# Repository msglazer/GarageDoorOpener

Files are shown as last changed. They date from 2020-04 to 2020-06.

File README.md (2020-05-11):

# GarageDoorOpener
Garage door opener keyfob replacement that can detect door position and allows for OK google commands. As well as a distance sensor and LEDs to show distance from garage wall.

## Hardware:
### Power Board

Features:
* 120V AC/DC converter to 24V, 20W output
* Two reed switch connectors 
* One relay control connector
* RJ45 connector for cable to control board

### Control Board

Features:
* Particle Boron Microcontroller with cellular connectivity
* 24V to 5W switching regulator
* ToF sensor for range finding
* LED header for visualizing distance
* RJ45 connector for power/control

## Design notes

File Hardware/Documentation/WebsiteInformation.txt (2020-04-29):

https://www.smps.us/pcbtracespacing.html - AC Creepage/Spacing Information
https://www.amazon.com/Aleph-DC-1561-Surface-Magnetic-Contact/dp/B00LYCUSBY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 - Reed switch, magnet combo

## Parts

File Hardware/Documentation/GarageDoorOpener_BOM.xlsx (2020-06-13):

Board | Need | Number | Unit Qty | RefDes | Value | Manufacturer | Dist. Part # | Mfg Part # | Price Each | Total Price | Description | Package | Type | Datasheet
Control | Have | 1 | 1 | U1 | 4G MCU | Particle | 1878-1023-ND | BRN402 | 49.28 | 49.28 | BORON LTE Microcontroller | Feather | Thru-hole | https://media.digikey.com/pdf/Data%20Sheets/Particle%20PDFs/Boron_LTE_Web.pdf
Control | Need | 2 | 1 | U2 | Switching Regulator | Texas Instruments | 296-TPS56637RPARCT-ND | TPS56637RPAR | 3.50 | 3.50 | Buck Switching Regulator IC Positive Adjustable 0.6V 1 Output 6A 10-PowerVFQFN | 10-PowerVFQFN | SMD | http://www.ti.com/general/docs/suppproductinfo.tsp?distId=10
Control | Need | 3 | 1 | U3 | Solid State Relay | IXYS Integrated Circuits Division | CLA221-ND | CPC1002N | 1.08 | 1.08 | Solid State SPST-NO (1 Form A) 4-SOP (0.150", 3.81mm) | 4-SOP (0.150", 3.81mm) | SMD | http://www.ixysic.com/home/pdfs.nsf/www/CPC1002N.pdf/$file/CPC1002N.pdf
Control | Need | 4 | 1 | U4 | ToF Sensor | STMicroelectronics | 497-17764-1-ND | VL53L1CXV0FY/1 | 6.43 | 6.43 | Optical Sensor 157.480" (4m) I²C Output | LGA-12 | SMD | https://www.mouser.com/datasheet/2/389/dm00452094-1799360.pdf
Control | Need | 5 | 1 | U5 | Level Shifter | Texas Instruments | 296-22862-6-ND | TXB0102DCUR | 0.71 | 0.71 | Voltage Level Translator Bidirectional 1 Circuit 2 Channel 100Mbps 8-VSSOP | 8-VSSOP | SMD | http://www.ti.com/general/docs/suppproductinfo.tsp?distId=10
Control | Need | 6 | 2 | Q1,Q2 | NMOS FET | Diodes Inc | DMG1012T-7DICT-ND | DMG1012T-7 | 0.29 | 0.58 | N-Channel 20V 630mA (Ta) 280mW (Ta) Surface Mount SOT-523 | SOT-523 | SMD | https://www.diodes.com/assets/Datasheets/ds31783.pdf
Control | Need | 7 | 1 | Q3 | PMOS FET | Nexperia USA Inc. | 1727-2310-1-ND | PMV65XPEAR | 0.36 | 0.36 | P-Channel 20V 2.8A (Ta) 480mW (Ta), 6.25W (Tc) Surface Mount TO-236AB | SOT-23-3 | SMD | https://assets.nexperia.com/documents/data-sheet/PMV65XPEA.pdf
Control | Need | 8 | 1 | L1 | Switching regulator inductor | Taiyo Yuden | 587-2892-1-ND | NRS4018T3R3MDGJ | 0.29 | 0.29 | 3.3µH Shielded Wirewound Inductor 2A 66mOhm Max Nonstandard | 4mm x 4mm | SMD | https://www.yuden.co.jp/productdata/catalog/wound04_e.pdf
Control | Have | 9 | 1 | D1 | Green LED | Würth Elektronik | 732-4986-1-ND | 150080VS75000 | 0.18 | 0.18 | Green 570nm LED Indication - Discrete 2V 0805 (2012 Metric) | 0805 | SMD | https://katalog.we-online.de/led/datasheet/150080VS75000.pdf
Control | Have | 10 | 1 | D2 | Red LED | Würth Elektronik | 732-4985-1-ND | 150080SS75000 | 0.18 | 0.18 | Red 630nm LED Indication - Discrete 1.9V 0805 (2012 Metric) | 0805 | SMD | https://katalog.we-online.de/led/datasheet/150080SS75000.pdf
Control | Need | 11 | 3 | D3,D4,D5 | TVS diode array (2 channel) | Toshiba Semiconductor and Storage | DF3A5.6LFULFCT-ND | DF3A5.6LFU,LF | 0.29 | 0.87 | 3V (Typ) Clamp 5A (8/20µs) Ipp Tvs Diode Surface Mount 7-XSON (1.1x2.1) | 7-XSON | SMD | https://assets.nexperia.com/documents/data-sheet/PUSB3FR6.pdf
Control | Have? | 12 | 3 | C1,C2,C3 | 4.7uF 50V | Murata Electronics | 490-10751-1-ND | GRM21BR61H475KE51L | 0.41 | 1.23 | 4.7µF ±10% 50V Ceramic Capacitor X5R 0805 (2012 Metric) | 0805 | SMD | https://search.murata.co.jp/Ceramy/image/img/A01X/G101/ENG/GRM21BR61H475KE51-01.pdf
Control | Have? | 13 | 1 | C4 | 0.1uF 50V | KEMET | 399-7845-1-ND | C0603C104M5RACTU | 0.10 | 0.10 | 0.1µF ±20% 50V Ceramic Capacitor X7R 0603 (1608 Metric) | 0603 | SMD | https://api.kemet.com/component-edge/download/datasheet/C0603C104M5RACTU.pdf
Control | Have | 14 | 4 | C5,C6,C16,C17 | 1uF 10V | Samsung Electro-Mechanics | 1276-1182-1-ND | CL10A105KP8NNNC | 0.10 | 0.40 | 1µF ±10% 10V Ceramic Capacitor X5R 0603 (1608 Metric) | 0603 | SMD | https://media.digikey.com/pdf/Data%20Sheets/Samsung%20PDFs/CL10A105KP8NNNC_Spec.pdf
Control | Have | 15 | 2 | C7,C12 | 0.1uF 16V | KEMET | 399-1099-1-ND | C0603C104M4RACTU | 0.10 | 0.20 | 0.1µF ±20% 16V Ceramic Capacitor X7R 0603 (1608 Metric) | 0603 | SMD | https://api.kemet.com/component-edge/download/datasheet/C0603C104M4RACTU.pdf
Control | Have? | 16 | 1 | C8 | 100pF 10V | Würth Elektronik | 732-7922-1-ND | 885012206003 | 0.10 | 0.10 | 100pF ±10% 10V Ceramic Capacitor X7R 0603 (1608 Metric) | 0603 | SMD | https://katalog.we-online.de/pbs/datasheet/885012206003.pdf
Control | Have | 17 | 2 | C9,C10 | 22uF 10V | Taiyo Yuden | 587-5464-1-ND | LMK212BBJ226MG-T | 0.30 | 0.60 | 22µF ±20% 10V Ceramic Capacitor X5R 0805 (2012 Metric) | 0805 | SMD | https://ds.yuden.co.jp/TYCOMPAS/ut/detail?pn=LMK212BBJ226MG-T%20&u=M
Control | Have? | 18 | 2 | C11,C13 | 4.7uF 10V | Taiyo Yuden | 587-1441-1-ND | LMK107BJ475KA-T | 0.19 | 0.38 | 4.7µF ±10% 10V Ceramic Capacitor X5R 0603 (1608 Metric) | 0603 | SMD | https://ds.yuden.co.jp/TYCOMPAS/ut/detail?pn=LMK107BJ475KA-T%20%20&u=M
Control | Have | 19 | 2 | C14,C15 | 2.2uF Cap
Control | Need | 20 | 3 | R1,R3,R4 | 649 ohm 1% | Stackpole Electronics | RMCF0603FT649RCT-ND | RMCF0603FT649R | 0.10 | 0.30 | 649 Ohms ±1% 0.1W, 1/10W Chip Resistor 0603 (1608 Metric) Automotive AEC-Q200 Thick Film | 0603 | SMD | https://www.seielect.com/catalog/sei-rmcf_rmcp.pdf
Control | Have | 21 | 11 | R2,R5,R6,R7,R9,R14,R15,R24,R26,R28 | 10K ohm 5% | Stackpole Electronics | RMCF0603JT10K0CT-ND | RMCF0603JT10K0 | 0.10 | 1.10 | 10 kOhms ±5% 0.1W, 1/10W Chip Resistor 0603 (1608 Metric) Automotive AEC-Q200 Thick Film | 0603 | SMD | https://www.seielect.com/catalog/sei-packaging.pdf
Control | Have | 22 | 1 | R11 | 10K ohm 1% | Yageo | 311-10.0KHRCT-ND | RC0603FR-0710KL | 0.10 | 0.10 | 10 kOhms ±1% 0.1W, 1/10W Chip Resistor 0603 (1608 Metric) Moisture Resistant Thick Film | 0603 | SMD | https://www.yageo.com/upload/media/product/productsearch/datasheet/rchip/PYu-RC_Group_51_RoHS_L_10.pdf
Control | Need | 23 | 1 | R8 | 20K ohm 1% | Yageo | 311-20.0KHRCT-ND | RC0603FR-0720KL | 1.00 | 1.00 | RES SMD 20K OHM 1% 1/10W 0603 | 0603 | SMD | https://www.yageo.com/upload/media/product/productsearch/datasheet/rchip/PYu-RC_Group_51_RoHS_L_10.pdf
Control | Need | 24 | 1 | R10 | 73.2K ohm 1% | KOA Speer Electronics, Inc. | 2019-RK73H1JTTD7322FCT-ND | RK73H1JTTD7322F | 0.10 | 0.10 | 73.2 kOhms ±1% 0.1W, 1/10W Chip Resistor 0603 (1608 Metric) Automotive AEC-Q200, Moisture Resistant Thick Film | 0603 | SMD | http://www.koaspeer.com/pdfs/RK73H.pdf
Control | Have | 25 | 2 | R12,R13 | 4.7K ohm 5% | Yageo | 311-4.7KGRCT-ND | RC0603JR-074K7L | 0.10 | 0.20 | 4.7 kOhms ±5% 0.1W, 1/10W Chip Resistor 0603 (1608 Metric) Moisture Resistant Thick Film | 0603 | SMD | https://www.yageo.com/upload/media/product/productsearch/datasheet/rchip/PYu-RC_Group_51_RoHS_L_10.pdf
Control | Have | 26 | 6 | R16,R17,R18,R19,R20,R21 | 0 ohm | Yageo | 311-0.0GRCT-ND | RC0603JR-070RL | 0.10 | 0.60 | 0 Ohms Jumper 0.1W, 1/10W Chip Resistor 0603 (1608 Metric) Moisture Resistant Thick Film | 0603 | SMD | https://www.yageo.com/upload/media/product/productsearch/datasheet/rchip/PYu-RC_Group_51_RoHS_L_10.pdf
Control | Have | 27 | 3 | R22.R23,R25 | 226 ohm
Control |  | 28 | 1 | J1 |  | LED header |  |  |  | 0.00
Control | Need | 29 | 1 | J2 | RJ45 Connector | Amphenol ICC (FCI) | 609-1046-ND | 54602-908LF | 0.62 | 0.62 | Jack Modular Connector 8p8c (RJ45, Ethernet) 90° Angle (Right) Unshielded Cat3 | RJ45 | Thru-hole | https://cdn.amphenol-icc.com/media/wysiwyg/files/documentation/datasheet/inputoutput/io_modularjack.pdf
Control | Need | 30 | 1 | PWR_IN1 | power inlet | Qualtek | Q840-ND | 770W-X2/13 | 0.77 | 0.77 | Power Entry Connector Receptacle, Male Pins IEC 320-C8 Panel Mount, Snap-In | 24.5x12.5 | Panel Mount | http://www.qualtekusa.com/images/AC_Receptacles/pdfs/770wx213.pdf
Control | Need | 31 | 1 | CABLE1 | 120V cord | Qualtek | Q536-ND | 223082-01 | 3.95 | 3.95 | 6.00' (1.83m) Power Cord Black NEMA 1-15P, Polarized To IEC 320-C7, Polarized SPT-2 | Cable | Thru-hole | http://www.qualtekusa.com/images/Power%20Cords/PDF%20Files/22308201.pdf
Control | Have | 32 | 1 | ANT1 | 4G antenna | Taoglas Limited | 931-1329-ND | FXUB63.07.0150C | 9.82 | 9.82 | 850MHz, 1.575GHz, 1.8GHz, 2.1GHz, 2.4GHz, 2.6GHz GPS, LTE, Wi-Fi Flat Patch RF Antenna 698MHz | flex PCB | UFL | https://cdn.taoglas.com/datasheets/FXUB63.07.0150C.pdf
Control | Have | 33 | 1 | PCB1 |  | OshPark |  |  | 11.25 | 11.25 |  | Rigid PCB
Control | Need | 34 | 1 | LEDSTRIP1 |  | SparkFun | COM-14015 |  | 8.03 | 8.03 | LED RGB Strip - Addressable, 1m (APA102)
Power | Need | 1 | 1 | PS1 |  | Mean Well USA | 1866-3040-ND | IRM-20-24 | 11.50 | 11.50 | Enclosed AC DC Converters 1 Uitgang 24V 900mA 85 ~ 264 VAC, 120 ~ 370 VDC Input | 4-DIP Module, 4 Leads | Thru-hole | https://www.meanwell.com/Upload/PDF/IRM-20/IRM-20-SPEC.PDF
Power | Need | 2 | 1 | J1 | 2pin AC Input | Phoenix Contact | 277-1721-ND | 1984617 | 0.48 | 0.48 | 2 Position Wire to Board Terminal Block Horizontal with Board 0.138" (3.50mm) Through Hole | 3.5mm pitch | Thru-hole | https://media.digikey.com/pdf/Data%20Sheets/Phoenix%20Contact%20PDFs/Combicon%20Compact%20Series.pdf
Power | Have? | 3 | 3 | J2,J3,J4 | 2pin JST | JST Sales America Inc | 455-1719-ND | S2B-PH-K-S(LF)(SN) | 0.17 | 0.51 | Connector Header Through Hole, Right Angle 2 position 0.079" (2.00mm) | 2pin | Thru-hole | http://www.jst-mfg.com/product/pdf/eng/ePH.pdf
Power | Need | 4 | 1 | J3 | RJ45 Connector | Amphenol ICC (FCI) | 609-1046-ND | 54602-908LF | 0.62 | 0.62 | Jack Modular Connector 8p8c (RJ45, Ethernet) 90° Angle (Right) Unshielded Cat3 | RJ45 | Thru-hole | https://cdn.amphenol-icc.com/media/wysiwyg/files/documentation/datasheet/inputoutput/io_modularjack.pdf
Power | Need | 5 | 4 | C1,C2,C3,C4 | 22uF 35V | TDK Corporation | 445-8045-1-ND | C3216X5R1V226M160AC | 1.06 | 4.24 | 22µF ±20% 35V Ceramic Capacitor X5R 1206 (3216 Metric) | 1206 | SMD | https://product.tdk.com/info/en/catalog/datasheets/mlcc_commercial_general_en.pdf?ref_disty=digikey
Power | Have | 6 | 1 | R1 | 4.7k ohm 5% | Yageo | 311-4.7KGRCT-ND | RC0603JR-074K7L | 0.10 | 0.10 | 4.7 kOhms ±5% 0.1W, 1/10W Chip Resistor 0603 (1608 Metric) Moisture Resistant Thick Film | 0603 | SMD | https://www.yageo.com/upload/media/product/productsearch/datasheet/rchip/PYu-RC_Group_51_RoHS_L_10.pdf
Power | Have | 7 | 1 | D1 |  | Würth Elektronik | 732-4986-1-ND | 150080VS75000 | 0.18 | 0.18 | Green 570nm LED Indication - Discrete 2V 0805 (2012 Metric) | 0805 | SMD | https://katalog.we-online.de/led/datasheet/150080VS75000.pdf
Power | Have | 8 | 1 | PCB1 |  | OshPark |  |  | 11.25 | 11.25
 |  |  |  |  |  |  |  |  | Control Board | 85.03
 |  |  |  |  |  |  |  |  | Power Board | 28.88
 |  |  |  |  |  |  |  |  | Total Price | 113.914532

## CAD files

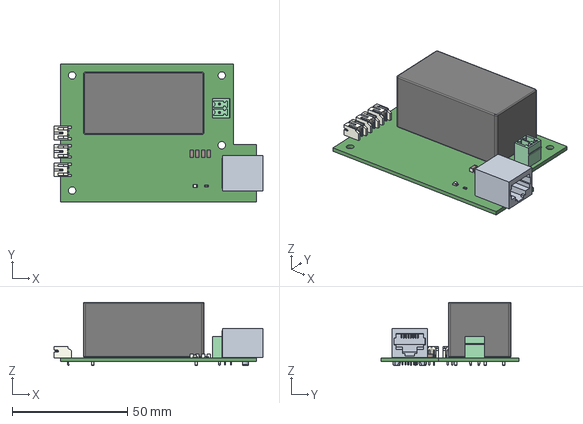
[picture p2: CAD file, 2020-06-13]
Hardware/PowerBoard/GarageDoorPowerBoard.step
90.8 x 60.0 x 27.6 mm

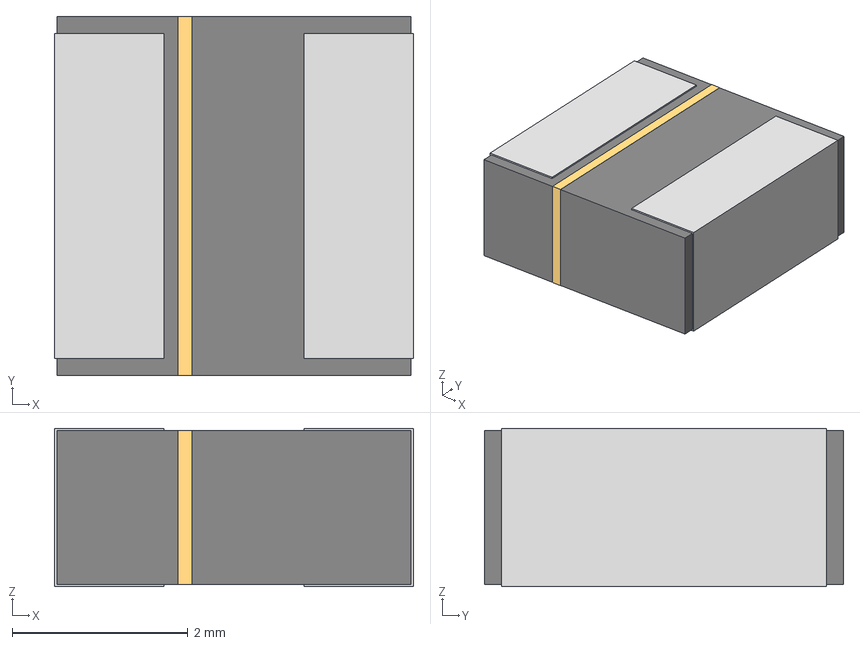
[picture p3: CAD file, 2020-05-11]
Hardware/Documentation/IND_TAIYO_NRS4018.step
4.09 x 4.09 x 1.80 mm

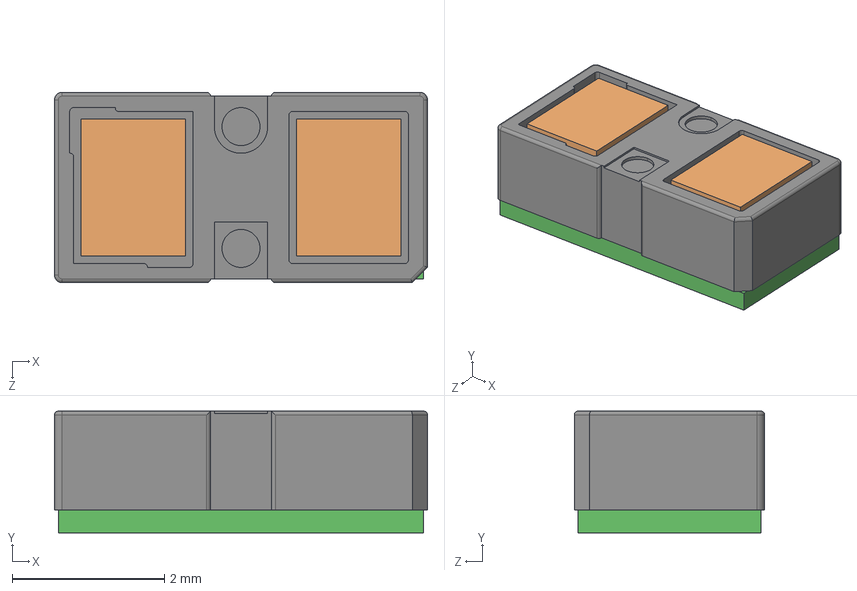
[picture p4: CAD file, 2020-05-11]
Hardware/Documentation/1--3DModel-STEP-56544.STEP
4.90 x 1.60 x 2.50 mm

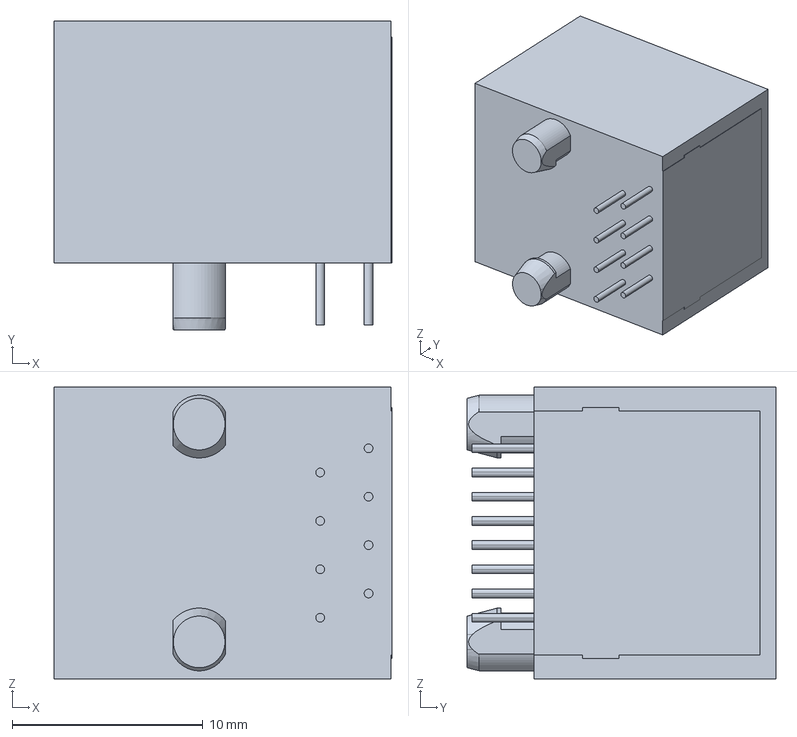
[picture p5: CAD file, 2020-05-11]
Hardware/Documentation/54602-908LFc.stp
17.7 x 16.2 x 15.3 mm

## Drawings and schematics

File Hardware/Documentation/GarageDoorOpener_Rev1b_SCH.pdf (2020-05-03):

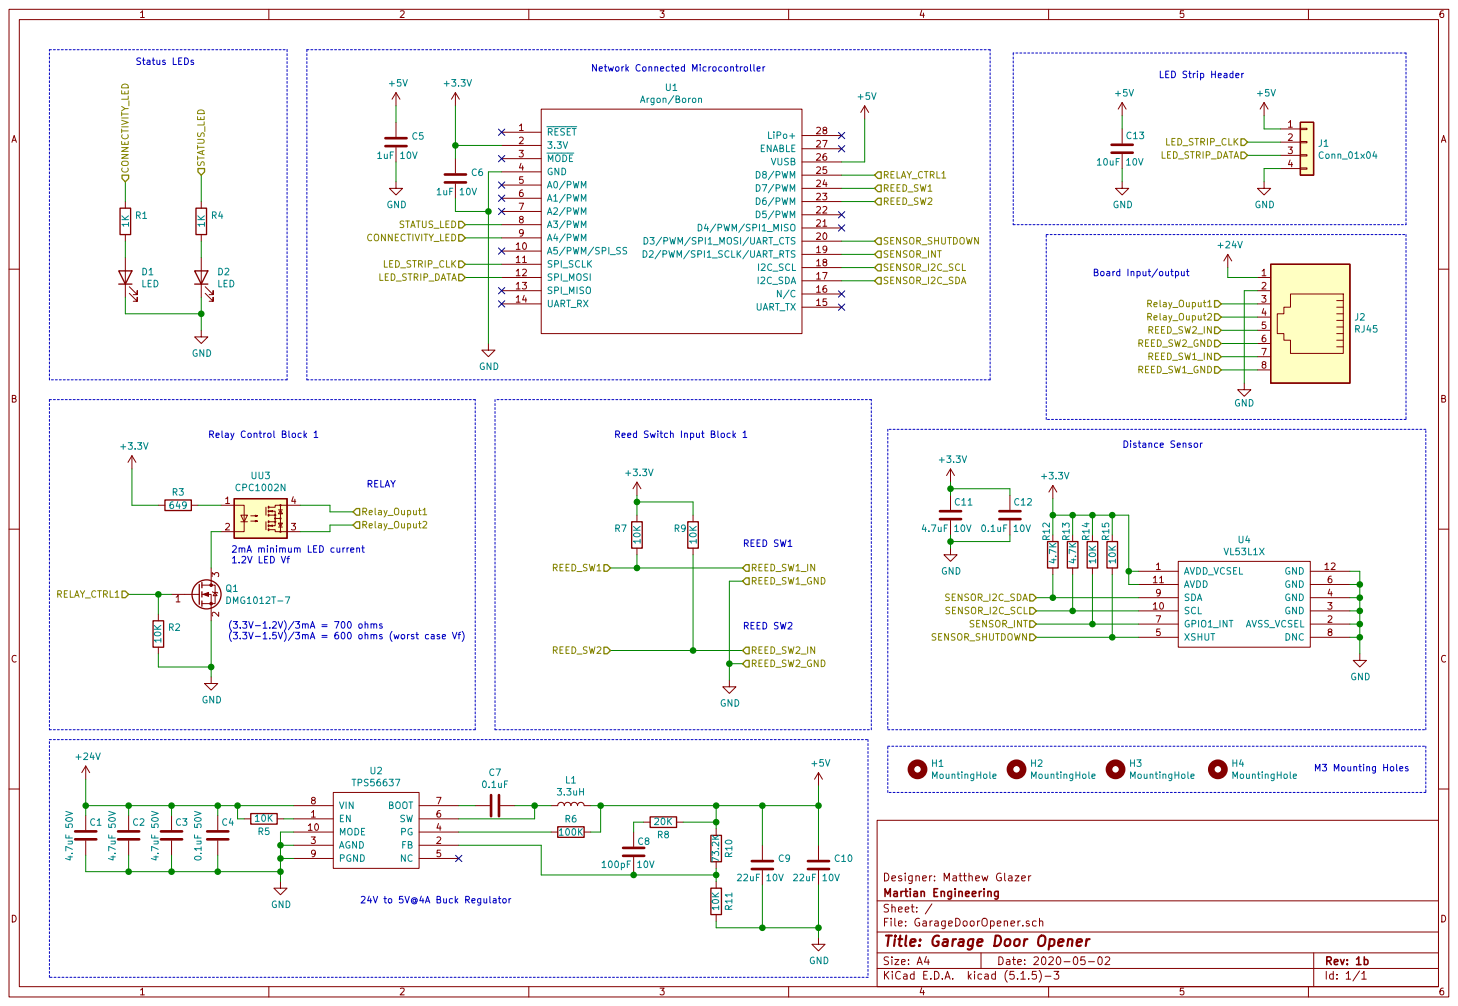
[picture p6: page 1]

4.7uF 10V GND
2mA minimum LED current 1.2V LED Vf (3.3V-1.2V)/3mA = 700 ohms

(3.3V-1.5V)/3mA = 600 ohms (worst case Vf)

File: GarageDoorOpener.sch Sheet: / Martian Engineering

Id: 1/1 Title: Garage Door Opener

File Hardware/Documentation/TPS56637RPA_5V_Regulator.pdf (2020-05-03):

## WEBENCH ® Design Report

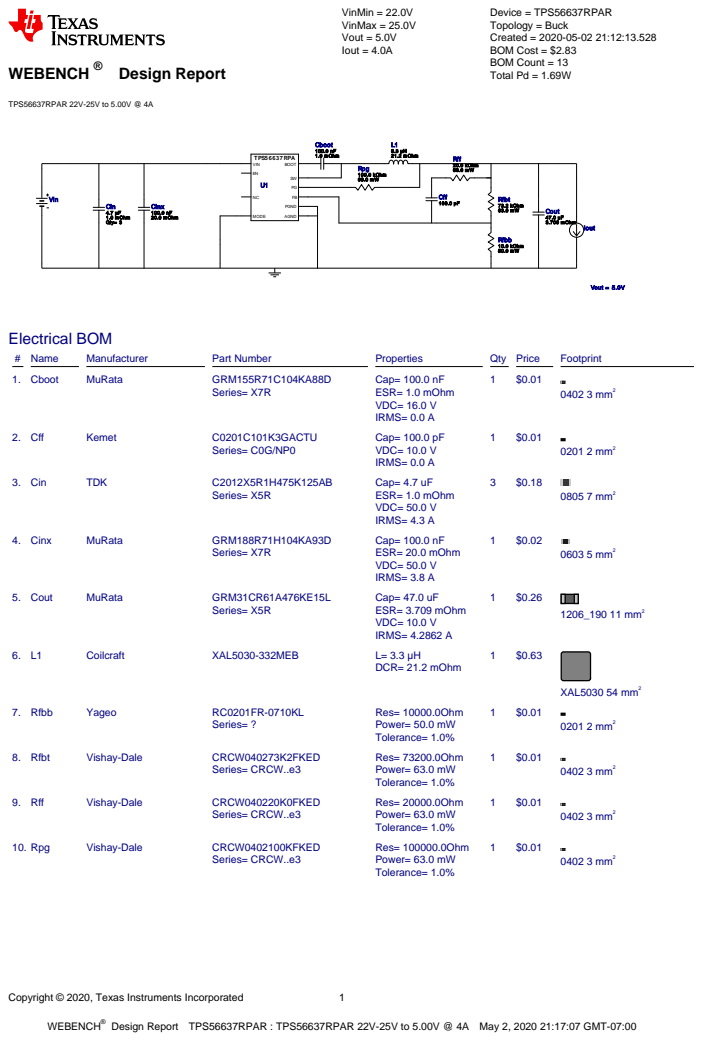
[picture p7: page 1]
Copyright © 2020, Texas Instruments Incorporated; WEBENCH®; TPS56637RPAR 22V-25V to 5.00V @ 4A; VinMin = 22.0V VinMax = 25.0V Vout = 5.0V Iout = 4.0A; Device = TPS56637RPAR Topology = Buck Created = 2020-05-02 21:12:13.528 BOM Cost = $2.83 BOM Count = 13 Total Pd = 1.69W; Cinx 100.0 nF 20.0 mOhm; TPS56637RPA; AGND; VIN; BOOT; PGND; MODE; Cin 4.7 µF 1.0 mOhm Qty= 3; Cout 47.0 µF 3.709 mOhm; Rfbb 10.0 kOhm 50.0 mW; Rfbt 73.2 kOhm 63.0 mW; L1 3.3 µH 21.2 mOhm; Cff 100.0 pF; Rff 20.0 kOhm 63.0 mW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

Design Report TPS56637RPAR : TPS56637RPAR 22V-25V to 5.00V @ 4A May 2, 2020 21:17:07 GMT-07:00

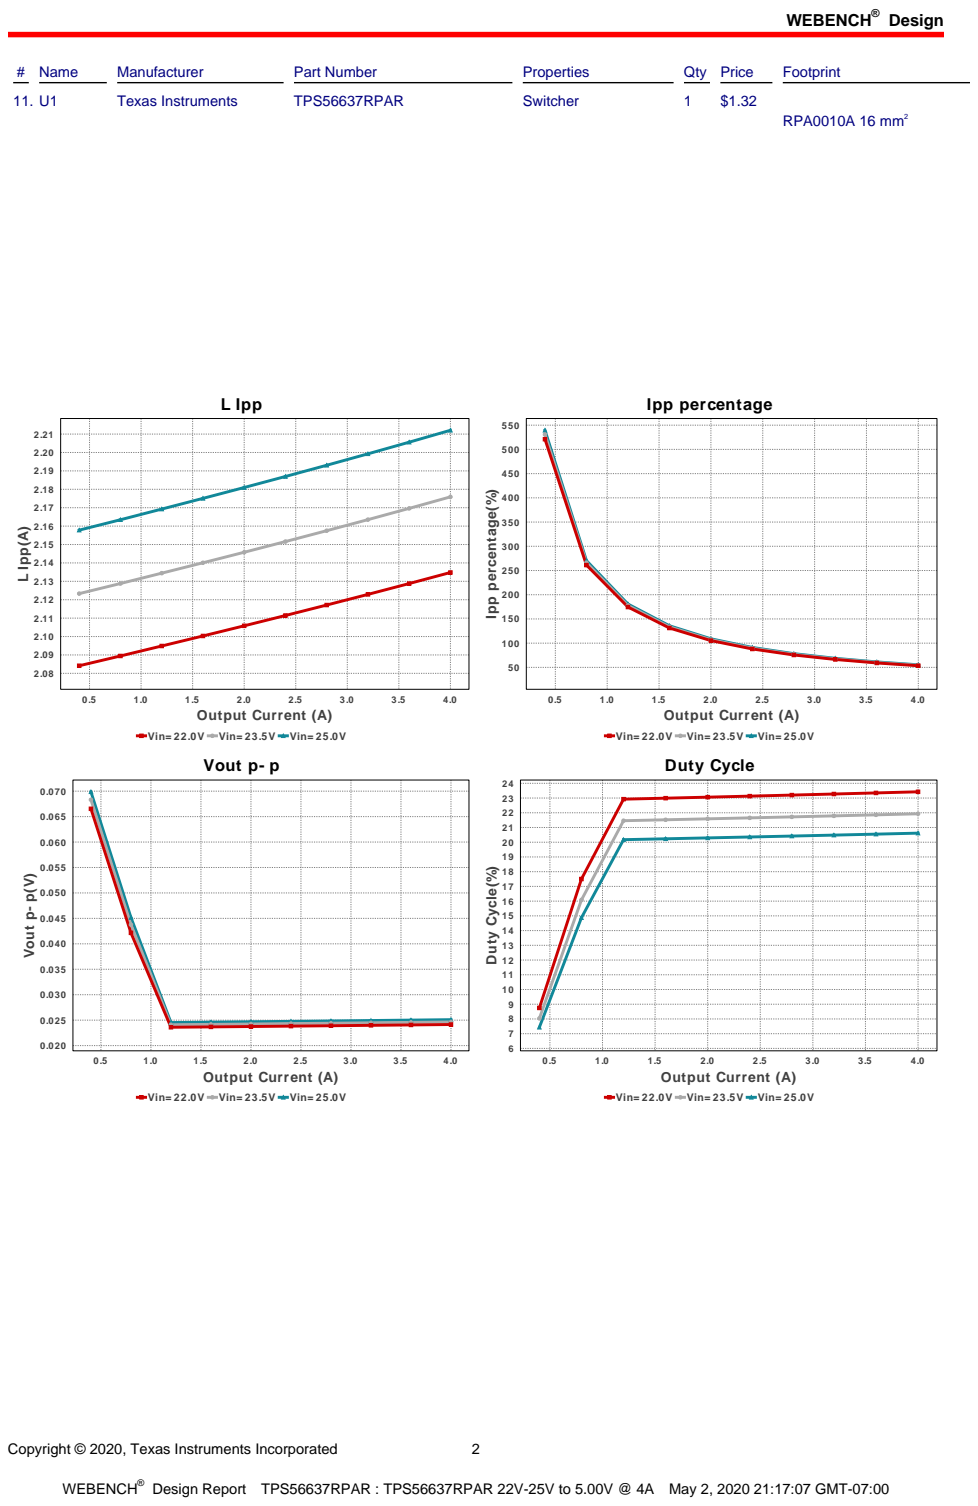
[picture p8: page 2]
Design; # Name; Manufacturer; Part Number; Properties; Qty Price; Footprint; Texas Instruments; TPS56637RPAR; Switcher; RPA0010A 16 mm²; L Ipp; 4.0 Output Current (A); L Ipp(A); Ipp percentage; Ipp percentage(%); Vout p- p(V); Duty Cycle(%)

Vin= 22.0V Vin= 23.5V Vin= 25.0V
Vout p- p

Duty Cycle

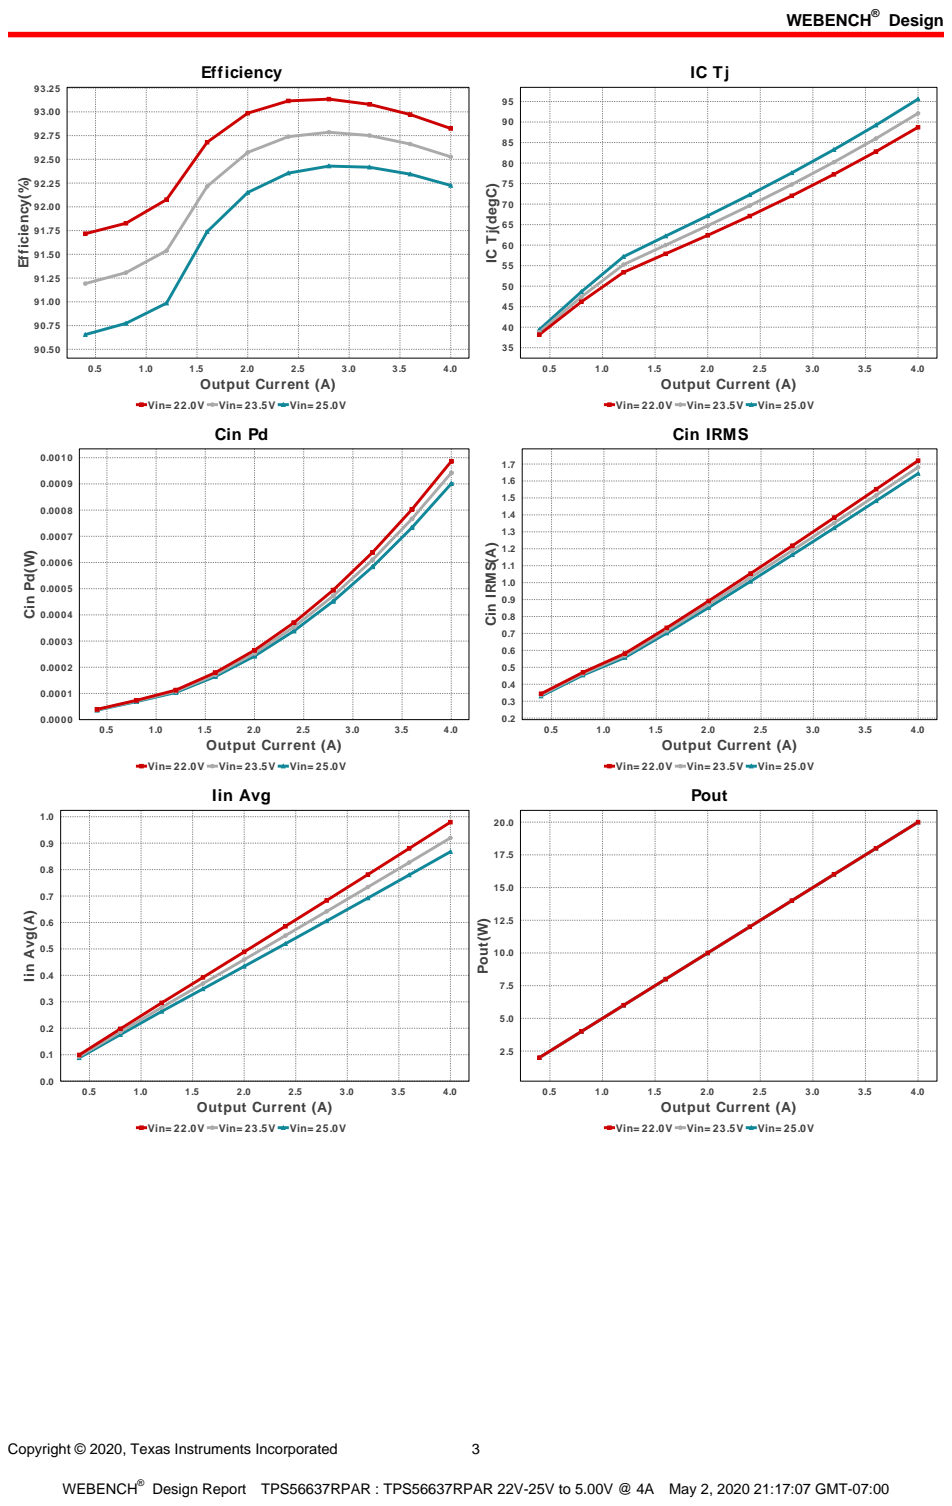
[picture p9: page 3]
Efficiency; 4.0 Output Current (A); Efficiency(%); Cin Pd; Cin Pd(W); Cin IRMS(A); Iin Avg; Iin Avg(A); Pout; Pout(W)

IC Tj(degC)

Vin= 22.0V Vin= 23.5V Vin= 25.0V

Cin IRMS

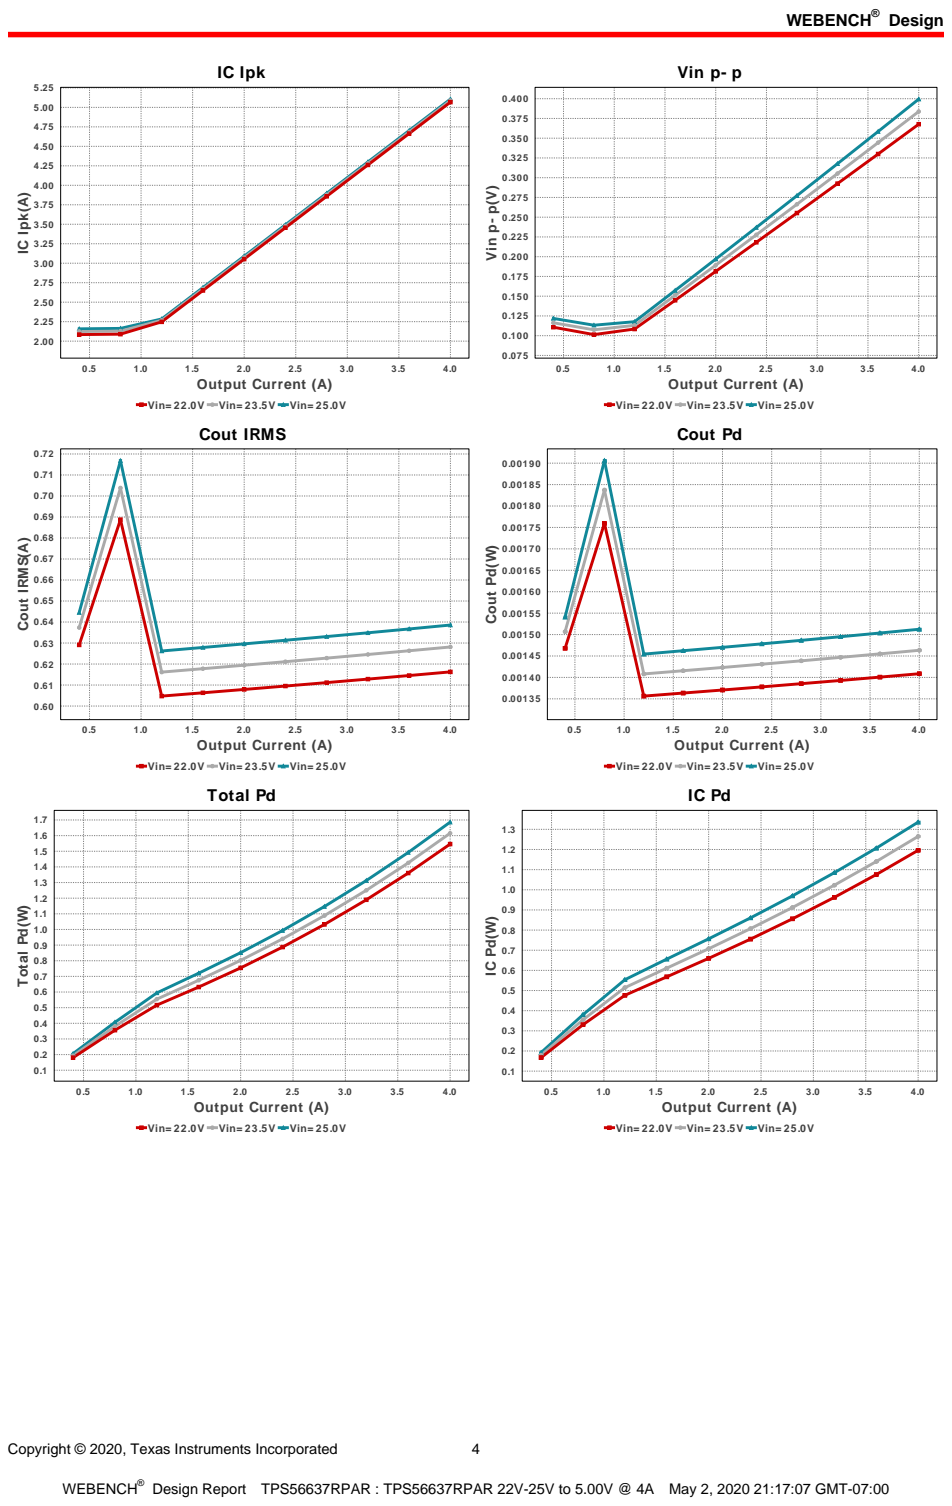
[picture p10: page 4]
IC Ipk; 4.0 Output Current (A); IC Ipk(A); Vin p- p; Vin p- p(V); Cout IRMS(A); Cout Pd; Cout Pd(W); Total Pd; Total Pd(W)

Vin= 22.0V Vin= 23.5V Vin= 25.0V
Cout IRMS

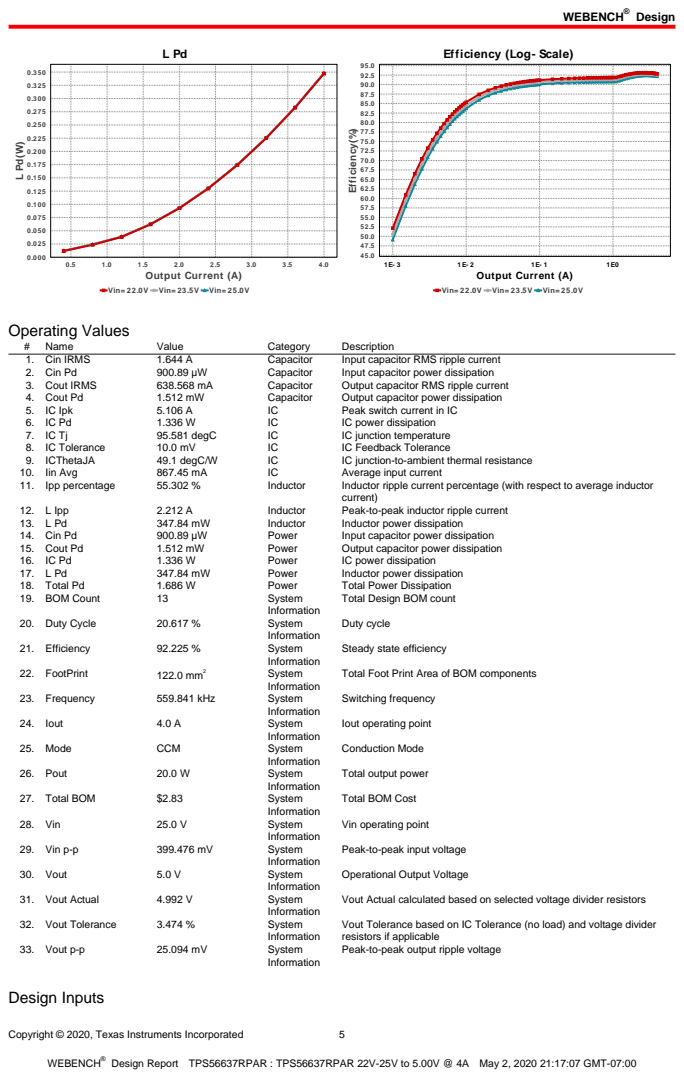
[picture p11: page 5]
4.0 Output Current (A); 1E0 Output Current (A); Efficiency(%); Operating Values; Name; Value; Category; Description; 1. Cin IRMS; Capacitor; Input capacitor RMS ripple current; 2. Cin Pd; Input capacitor power dissipation; 3. Cout IRMS; Output capacitor RMS ripple current; 4. Cout Pd; Output capacitor power dissipation; 5. IC Ipk; Peak switch current in IC; IC power dissipation; 95.581 degC; IC junction temperature; 8. IC Tolerance; IC Feedback Tolerance; 9. ICThetaJA; 49.1 degC/W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

Efficiency (Log- Scale)

Vin= 22.0V Vin= 23.5V Vin= 25.0V

Total Design BOM count

Steady state efficiency

Total Foot Print Area of BOM components

Iout operating point

Total output power

Total BOM Cost

Vin operating point

Peak-to-peak input voltage

Operational Output Voltage

Vout Actual calculated based on selected voltage divider resistors

Vout Tolerance based on IC Tolerance (no load) and voltage divider
resistors if applicable
Peak-to-peak output ripple voltage

# | Name | Value | Description

1. Iout | 4.0 | Maximum Output Current
2. VinMax | 25.0 | Maximum input voltage
3. VinMin | 22.0 | Minimum input voltage
4. Vout | 5.0 | Output Voltage
5. acFrequency | 60.0 | AC Frequency
6. base_pn | TPS56637 | Base Product Number
7. source | DC | Input Source Type
8. Ta | 30.0 | Ambient temperature

## Design Assistance

1. TPS56637 Product Folder : http://www.ti.com/product/TPS56637 : contains the data sheet and other resources.

Important Notice and Disclaimer

TI provides technical and reliability data (including datasheets), design resources (including reference designs), application or other design advice, web tools, safety information, and other resources AS IS and with all faults, and disclaims all warranties. These resources are intended for skilled developers designing with TI products. You are solely responsible for (1) selecting the appropriate TI products for your application, (2) designing, validating and testing your application, and (3) ensuring your application meets applicable standards, and any other safety, security, or other requirements.

These resources are subject to change without notice. TI grants you permission to use these resources only for development of an application that uses the TI products described in the resource. Other reproduction and display of these resources is prohibited. No license is granted to any other TI intellectual property right or to any third party intellectual property right. TI disclaims responsibility for, and you will fully indemnify TI and its representatives against, any claims, damages, costs, losses, and liabilities arising out of your use of these resources.

Providing these resources does not expand or otherwise alter TI's applicable Terms of Sale or other applicable terms available either on ti.com or provided in conjunction with TI products.

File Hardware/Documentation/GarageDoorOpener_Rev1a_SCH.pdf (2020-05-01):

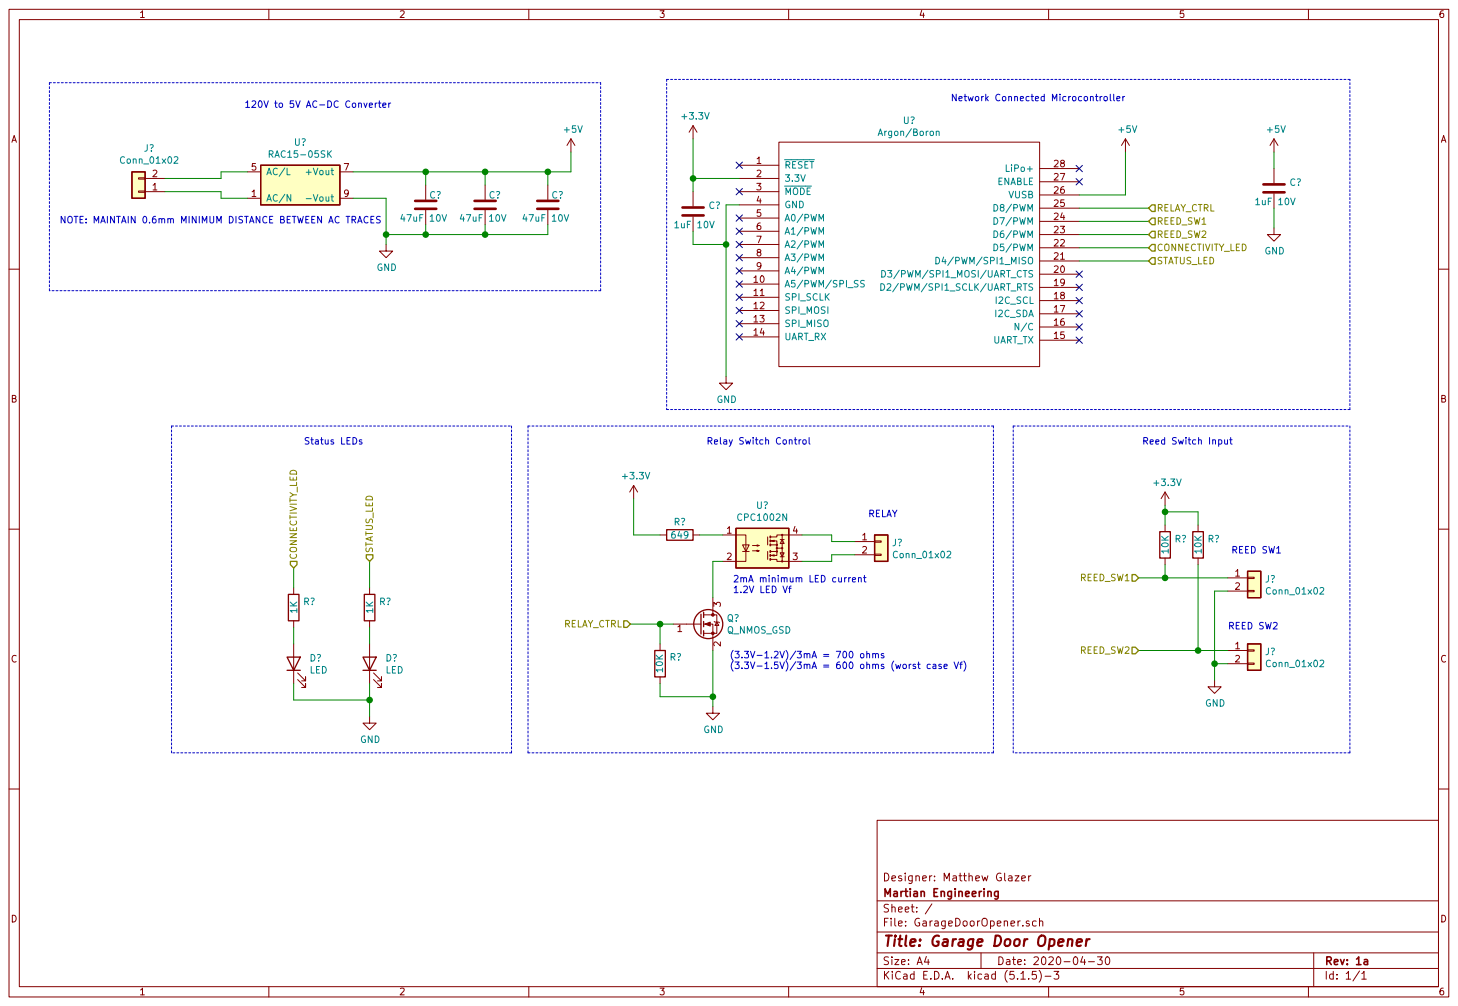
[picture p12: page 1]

120V to 5V AC-DC Converter

REED_SW1 RELAY_CTRL RELAY_CTRL NOTE: MAINTAIN 0.6mm MINIMUM DISTANCE BETWEEN AC TRACES

File: GarageDoorOpener.sch Sheet: / Martian Engineering

Id: 1/1 Title: Garage Door Opener

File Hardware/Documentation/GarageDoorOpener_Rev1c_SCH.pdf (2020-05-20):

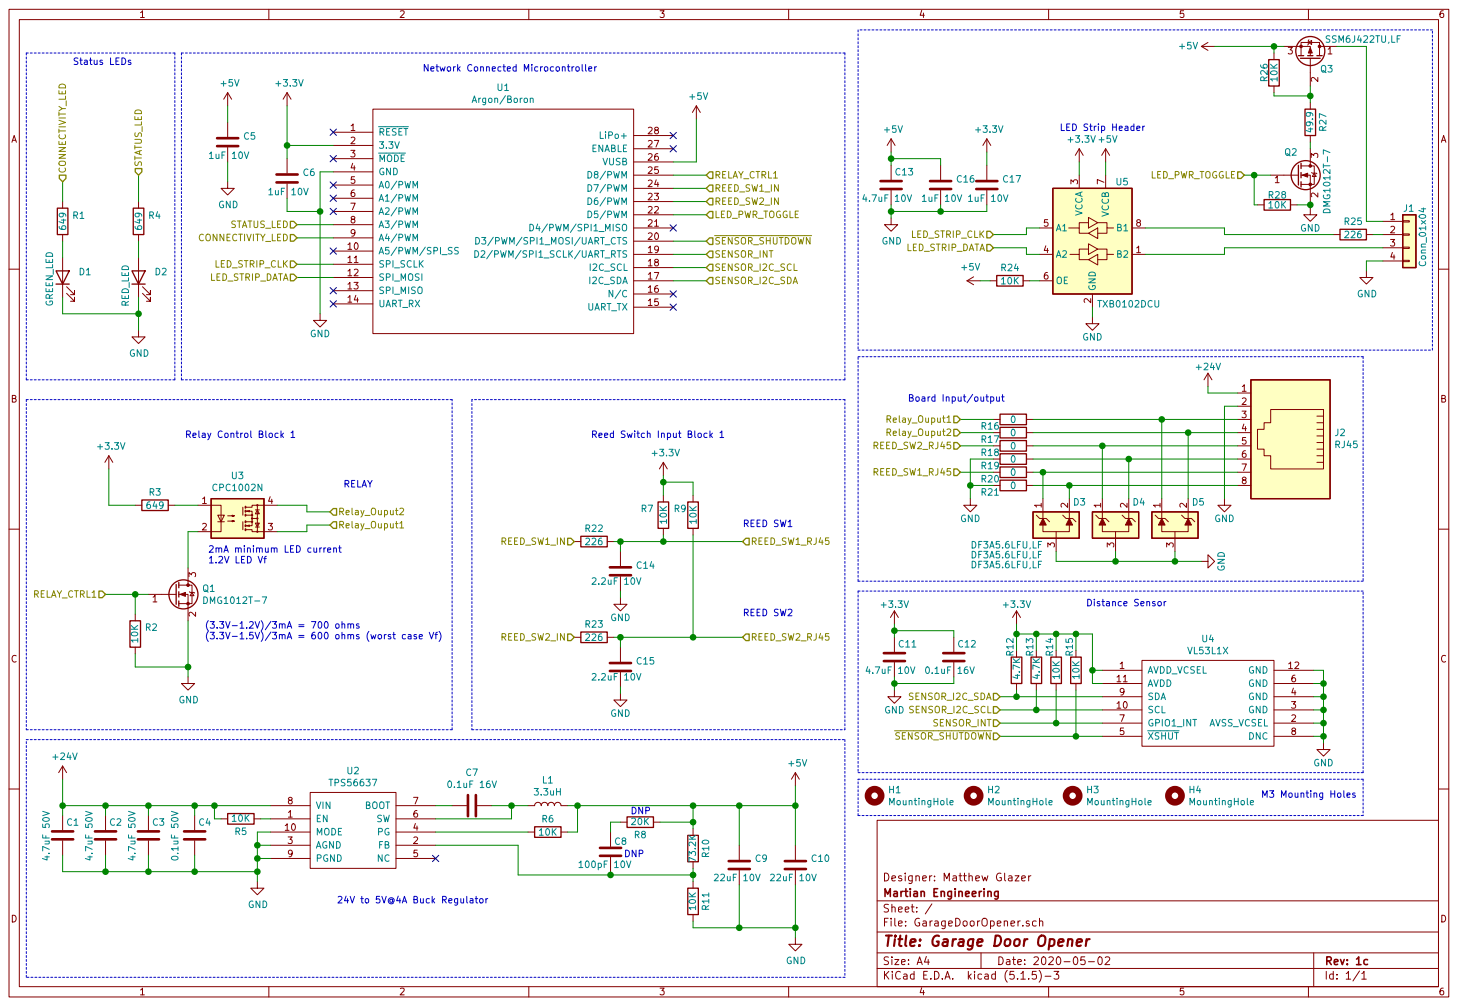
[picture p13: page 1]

Designer: Matthew Glazer
File: GarageDoorOpener.sch Sheet: / Martian Engineering

Id: 1/1 Title: Garage Door Opener

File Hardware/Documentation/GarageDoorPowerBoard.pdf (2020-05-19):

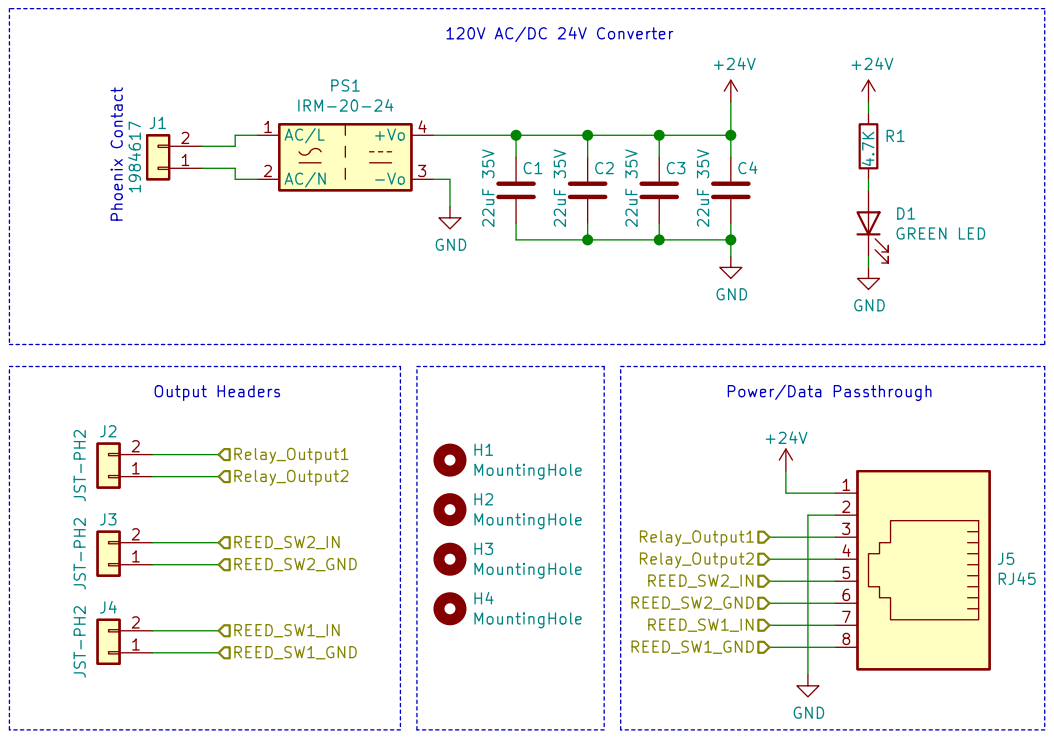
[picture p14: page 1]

File: GarageDoorPowerBoard.sch Sheet: /
Id: 1/1 Title:

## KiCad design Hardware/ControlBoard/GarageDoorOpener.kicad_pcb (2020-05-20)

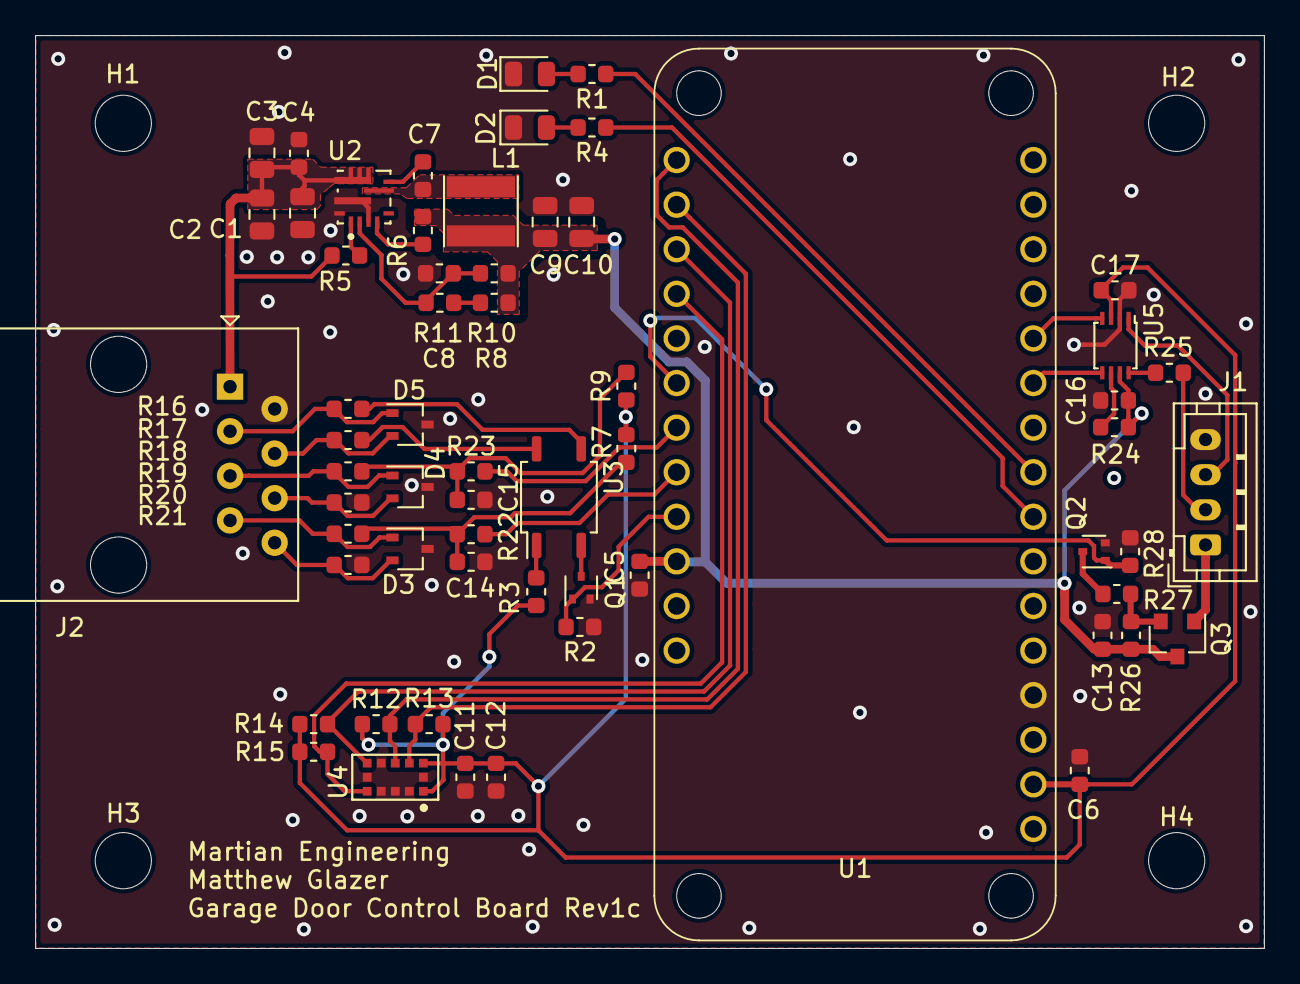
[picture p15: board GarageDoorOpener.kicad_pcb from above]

Board: 2 copper layers, 70.0 x 52.0 mm, 65 parts (0 on the bottom side), 43 nets.

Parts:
C1, C2, C3: 4.7uF 50V; C_0805_2012Metric
C4: 0.1uF 50V; C_0603_1608Metric
C5, C6, C16, C17: 1uF 10V; C_0603_1608Metric
C7, C12: 0.1uF 16V; C_0603_1608Metric
C8: 100pF 10V; C_0603_1608Metric
C9, C10: 22uF 10V; C_0805_2012Metric
C11, C13: 4.7uF 10V; C_0603_1608Metric
C14, C15: 2.2uF 10V; C_0603_1608Metric
D1: GREEN_LED; LED_0805_2012Metric
D2: RED_LED; LED_0805_2012Metric
D3, D4, D5: DF3A5.6LFU,LF; SOT-323_SC-70
H1, H2, H3, H4: MountingHole; MountingHole_3.2mm_M3
J1: Conn_01x04; JST_PH_B4B-PH-K_1x04_P2.00mm_Vertical
J2: RJ45; RJ45_Amphenol_54602-x08_Horizontal
L1: 3.3uH; L_Taiyo-Yuden_NR-40xx
Q1, Q2: DMG1012T-7; SOT-523
Q3: SSM6J422TU,LF; SOT-23
R1, R3, R4: 649; R_0603_1608Metric
R2, R5, R6, R7, R9, R11, R14, R15, R24, R26, R28: 10K; R_0603_1608Metric
R8: 20K; R_0603_1608Metric
R10: 73.2K; R_0603_1608Metric
R12, R13: 4.7K; R_0603_1608Metric
R16, R17, R18, R19, R20, R21: 0; R_0603_1608Metric
R22, R23, R25: 226; R_0603_1608Metric
R27: 49.9; R_0603_1608Metric
U1: Argon/Boron; ParticleBoron
U2: TPS56637; TPS56637RPAR
U3: CPC1002N; SOP-4_3.8x4.1mm_P2.54mm
U4: VL53L1X; VL53L1CXV0FY_1
U5: TXB0102DCU; VSSOP-8_2.4x2.1mm_P0.5mm

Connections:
+3V3: C6.1, C11.1, C12.1, C17.1, R3.2, R7.1, R9.1, R12.1, R13.1, R14.1, R15.1, U1.2, U4.1, U4.11, U5.3
+5V: C5.1, C9.2, C10.2, C13.1, C16.1, L1.2, Q3.3, R6.1, R8.2, R10.2, R24.2, R26.1, U1.26, U5.7
+24V: C1.1, C2.1, C3.1, C4.1, J2.1, R5.1, U2.8
/CONNECTIVITY_LED: R1.1, U1.9
/LED_PWR_TOGGLE: Q2.1, R28.2, U1.22
/LED_STRIP_CLK: U1.11, U5.5
/LED_STRIP_DATA: U1.12, U5.4
/REED_SW1_IN: R22.2, U1.24
/REED_SW1_RJ45: C14.1, R7.2, R20.2, R22.1
/REED_SW2_IN: R23.2, U1.23
/REED_SW2_RJ45: C15.1, R9.2, R18.2, R23.1
/RELAY_CTRL1: Q1.1, R2.2, U1.25
/Relay_Ouput1: R16.2, U3.3
/Relay_Ouput2: R17.2, U3.4
/SENSOR_I2C_SCL: R13.2, U1.18, U4.10
/SENSOR_I2C_SDA: R12.2, U1.17, U4.9
/SENSOR_INT: R14.2, U1.19, U4.7
/STATUS_LED: R4.1, U1.8
/~SENSOR_SHUTDOWN: R15.2, U1.20, U4.5
GND: C1.2, C2.2, C3.2, C4.2, C5.2, C6.2, C9.1, C10.1, C11.2, C12.2, C13.2, C14.2, C15.2, C16.2, C17.2, D1.1, D2.1, D3.3, D4.3, D5.3, J1.4, J2.2, Q1.2, Q2.2, R2.1, R11.1, R19.2, R21.2, R28.1, U1.4, U2.3, U2.9, U2.10, U4.2, U4.3, U4.4, U4.6, U4.8, U4.12, U5.2
unnamed: C7.1, L1.1, U2.6
unnamed: C7.2, U2.7
unnamed: C8.1, R10.1, R11.2, U2.2
unnamed: C8.2, R8.1
unnamed: D1.2, R1.2
unnamed: D2.2, R4.2
unnamed: D3.1, J2.7, R20.1
unnamed: D3.2, J2.8, R21.1
unnamed: D4.1, J2.5, R18.1
unnamed: D4.2, J2.6, R19.1
unnamed: D5.1, J2.3, R16.1
unnamed: D5.2, J2.4, R17.1
unnamed: J1.1, Q3.1
unnamed: J1.2, R25.1
unnamed: J1.3, U5.1
unnamed: Q1.3, U3.2
unnamed: Q2.3, R27.1
unnamed: Q3.2, R26.2, R27.2
unnamed: R3.1, U3.1
unnamed: R5.2, U2.1
unnamed: R6.2, U2.4
unnamed: R24.1, U5.6
unnamed: R25.2, U5.8

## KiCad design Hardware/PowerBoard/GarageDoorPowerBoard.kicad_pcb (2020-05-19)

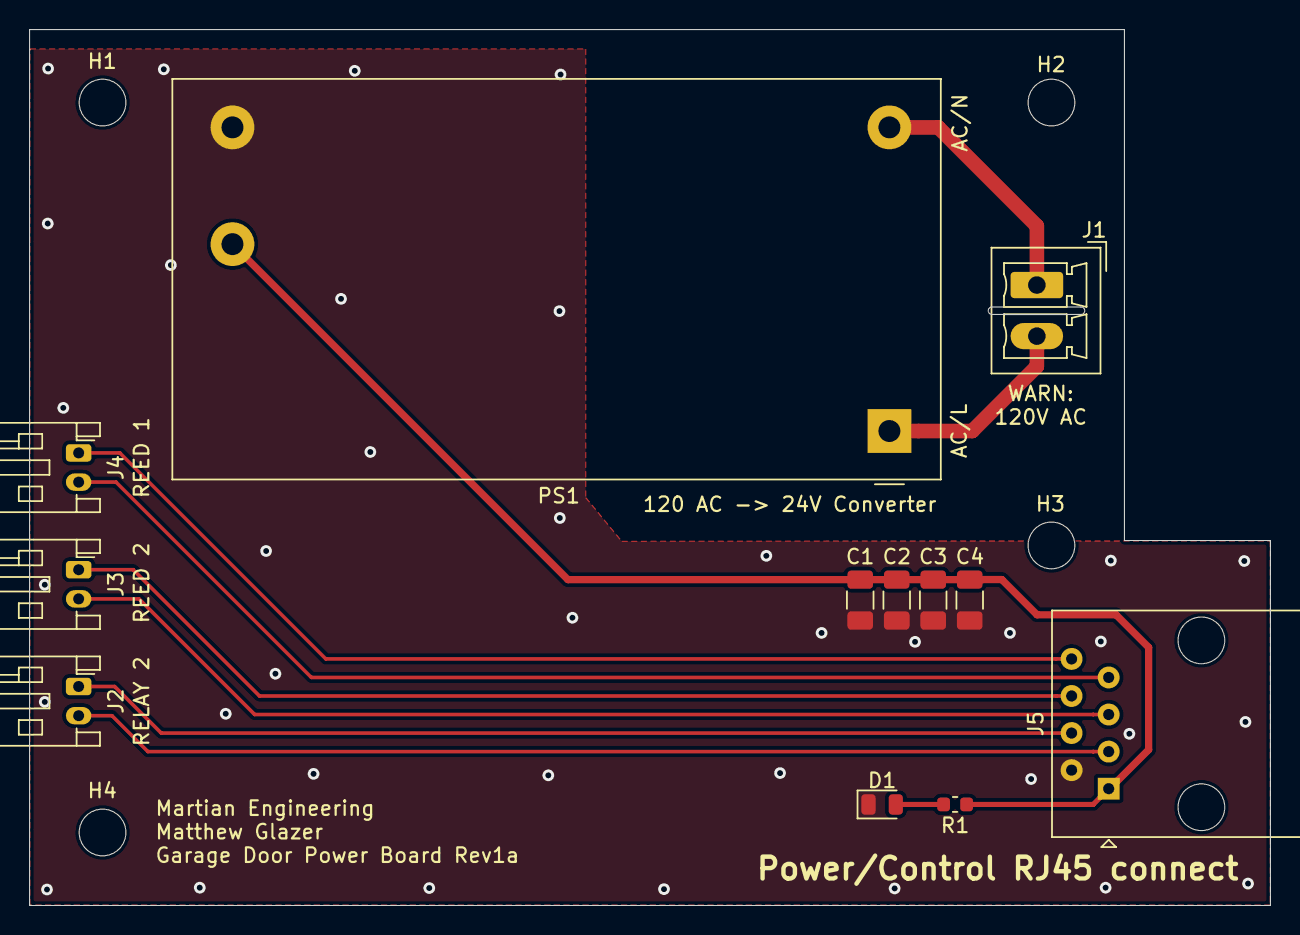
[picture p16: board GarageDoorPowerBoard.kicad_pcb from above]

Board: 2 copper layers, 85.0 x 60.0 mm, 16 parts (0 on the bottom side), 11 nets.

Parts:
C1, C2, C3, C4: 22uF 35V; C_1206_3216Metric
D1: GREEN LED; LED_0805_2012Metric
H1, H2, H3, H4: MountingHole; MountingHole_3.2mm_M3
J1: 1984617; PhoenixContact_MCV_1,5_2-G-3.5_1x02_P3.50mm_Vertical
J2, J3, J4: JST-PH2; JST_PH_S2B-PH-K_1x02_P2.00mm_Horizontal
J5: RJ45; RJ45_Amphenol_54602-x08_Horizontal
PS1: IRM-20-24; Converter_ACDC_MeanWell_IRM-20-xx_THT
R1: 4.7K; R_0603_1608Metric

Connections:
+24V: C1.1, C2.1, C3.1, C4.1, J5.1, PS1.4, R1.1
/REED_SW1_GND: J4.1, J5.8
/REED_SW1_IN: J4.2, J5.7
/REED_SW2_GND: J3.1, J5.6
/REED_SW2_IN: J3.2, J5.5
/Relay_Output1: J2.2, J5.3
/Relay_Output2: J2.1, J5.4
GND: C1.2, C2.2, C3.2, C4.2, D1.1, J5.2, PS1.3
unnamed: D1.2, R1.2
unnamed: J1.1, PS1.2
unnamed: J1.2, PS1.1

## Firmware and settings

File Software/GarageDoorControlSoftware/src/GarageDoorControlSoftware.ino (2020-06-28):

/*
 * Project GarageDoorControlSoftware
 * Description: control my garage door
 * Author: Matthew Glazer
 * Date: 6/27/2020
 */

#include <Wire.h>
#include "SparkFun_VL53L1X.h"
#include "application.h"
#include "dotstar.h"

#define NUMPIXELS 30

#define DATAPIN   D12
#define CLOCKPIN  D13
Adafruit_DotStar strip = Adafruit_DotStar(NUMPIXELS, DATAPIN, CLOCKPIN);

SFEVL53L1X distanceSensor;
//Uncomment the following line to use the optional shutdown and interrupt pins.
//SFEVL53L1X distanceSensor(Wire, SHUTDOWN_PIN, INTERRUPT_PIN);

#define LEDPOWERPIN  D5
#define RELAY_CTRL   D8
#define REED_SW1     D7
#define REED_SW2     D6
#define LED1         A3
#define LED2         A4
#define GARAGEDOORSTATE 0

// setup() runs once, when the device is first turned on.
void setup() 
{
  strip.begin(); // Initialize pins for output
  strip.show();  // Turn all LEDs off ASAP

  pinMode(RELAY_CTRL, OUTPUT);
  pinMode(REED_SW1, INPUT);
  pinMode(REED_SW2, INPUT);
  pinMode(LEDPOWERPIN, OUTPUT);
  pinMode(LED1, OUTPUT);
  pinMode(LED2, OUTPUT);

  digitalWrite(RELAY_CTRL, LOW);
  digitalWrite(LEDPOWERPIN, LOW);
  digitalWrite(LED1, HIGH);
}

// loop() runs over and over again, as quickly as it can execute.
void loop() 
{
  // The core of your code will likely live here.
  LEDRangeFind(GARAGEDOORSTATE);
}





void LEDRangeFind(GARAGEDOORSTATE)
{
  if (GARAGEDOORSTATE = CLOSED)
  {
    digitalWrite(LEDPOWERPIN, LOW);
  }
  else if (GARAGEDOORSTATE = OPEN)
  {
    digitalWrite(LEDPOWERPIN, HIGH);
  }

  distanceSensor.startRanging(); //Write configuration bytes to initiate measurement
  while (!distanceSensor.checkForDataReady())
  {
    delay(1);
  }
  int distance = distanceSensor.getDistance(); //Get the result of the measurement from the sensor
  distanceSensor.clearInterrupt();
  distanceSensor.stopRanging();

  float distanceInches = distance * 0.0393701;
}

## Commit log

2020-04-28 Intital schematic started as well as some supporting documentation
    [GarageDoorOpener.kicad_pcb, GarageDoorOpener.sch, GarageDoorOpener_BOM.xlsx]
2020-04-29 small amount of work done, added some documentation
    [GarageDoorOpener.sch]
2020-05-01 first pass on the schematic done
    [GarageDoorOpener.sch, GarageDoorOpener_BOM.xlsx]
2020-05-01 Re-arranged the files in the repo
    [GarageDoorOpener.kicad_pcb, GarageDoorOpener.sch, GarageDoorOpener_BOM.xlsx]
2020-05-01 schematic slightly updated (footprint association) PCB started
    [GarageDoorOpener.sch, GarageDoorOpener_BOM.xlsx]
2020-05-03 scope creep is great, decided to expand on the project a bit, Rev1b
    [Control_Input.sch, Control_Output.sch, GarageDoorOpener.sch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]
2020-05-03 I moved files again, added the power board schematic, working on BoM
    [Control_Input.sch, Control_Output.sch, GarageDoorOpener.kicad_pcb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]
2020-05-05 Schematics done, PCBs have components dropped in and BoM finished
    [GarageDoorOpener.kicad_pcb, GarageDoorOpener.sch, GarageDoorOpener_BOM.xlsx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]
2020-05-07 started work on the power PCB, board shape and basic placement complete
    [GarageDoorPowerBoard.kicad_pcb, GarageDoorPowerBoard.sch]
2020-05-08 PCB finished for power board
    [GarageDoorPowerBoard.kicad_pcb]
2020-05-08 Power Board Gerbers!
    [GarageDoorPowerBoard-B_Cu.gbr, GarageDoorPowerBoard-B_Mask.gbr, GarageDoorPowerBoard-B_Paste.gbr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]
2020-05-09 working on the PCB for the control board
    [GarageDoorOpener.kicad_pcb, GarageDoorOpener.sch]
2020-05-10 placement of components 80% board outline done
    [GarageDoorOpener.kicad_pcb]
2020-05-10 first pass of completed control board done
    [GarageDoorOpener.kicad_pcb, GarageDoorOpener.sch]
2020-05-11 minor tweaks as I was making a readme
    [GarageDoorOpener.kicad_pcb, GarageDoorPowerBoard.kicad_pcb]
2020-05-11 CAD models and updated PCBs per readme changes (pictures)
    [1--3DModel-STEP-56544.STEP, 54602-908LFc.stp, GarageDoorOpener.kicad_pcb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]
2020-05-19 Power Board gerbers
    [GarageDoorPowerBoard-B_Cu.gbr, GarageDoorPowerBoard-B_Mask.gbr, GarageDoorPowerBoard-B_Paste.gbr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]
2020-05-19 minor tweaks, powerboard ready!
    [GarageDoorPowerBoard.kicad_pcb]
2020-05-19 added some bits to the schematic, BoM updated
    [GarageDoorOpener.kicad_pcb, GarageDoorOpener.sch, GarageDoorOpener_BOM.xlsx]
2020-05-20 Control Board Gerbers generated
    [GarageDoorOpener-B_Cu.gbr, GarageDoorOpener-B_Mask.gbr, GarageDoorOpener-B_Paste.gbr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]
2020-05-20 finished the control board, ordered PCBs!
    [GarageDoorOpener.kicad_pcb, GarageDoorOpener.sch, GarageDoorOpener_BOM.xlsx]
2020-06-13 added some step files
    [GarageDoorOpener_BOM.xlsx, GarageDoorPowerBoard.step]
